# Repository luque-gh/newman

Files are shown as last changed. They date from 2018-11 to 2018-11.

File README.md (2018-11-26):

# Newman alternative - Small scale without mechanical commutator 
## Introduction 
The objective of this project is to **reproduce some claims made by Joseph Newman about his energy machine**.
This will be done in a **smaller scale** compared to the big machine Newman demonstrated.
This machine follows most of Newman's design described in his book.

However, it runs in a much lower voltage **~190VDC** compared to the one demonstrated by Newman (1500+ VDC).
This lower voltage makes possible to use **mosfet transistor and zener diodes** instead of a mechanical commutator.
**Duty cycle and frequency are adjustable** to optimize the performance through a **555 timer**.
Since **Newman's claims timing is very critical** for his invention, this gives much more flexibility to optimize compared to a mechanical commutator.

## Working
**Infrared emitter and sensor are used inhibit or activate the FIRING/BLANK/SHORT OUT cycle** depending on current rotor position.
This machine uses **a solid-state circuit with a 555 timer** to alternate between **FIRING (HIGH)** and **BLANK / SHORT OUT (LOW)**.

### FIRING/BLANK/SHORT OUT Cycle
The first phase is **FIRING** which enable both mosfets to energise the coil through the battery bank.
After that, the **BLANK** phase begins and cut the supply energy from the batteries, collapsing the field from the coil.
The **BLANK** phase only ends when the voltage difference in the coil is above the reverse zener voltage (>400V).
When this voltage is achieved, the **SHORT OUT** begins.
After that, a new **FIRING** phase begins reconnecting the battery bank to the coil again.

The cycle is activated in the range 135° to 225° and determined by the printed part **Commutator-Disc-90Deg**.
Each activation range requires an independent coil and circuit. In the test setup and videos, only one coil is used, but it is possibile to use two coils and activate in the range -45° to 45° as well.

## Schematic

Created using **Fritzing 0.9.3**.

Available in **/schematic**.

## Test Setup
* One coil activated in the range 135° to 225°.
* **~190V VDC** input voltage for the coil (20 x 9V zinc-carbon batteries **OUT OF WARRANTY, BUT NOT DEPLETED**).
* 9V zinc-cabon battery for the circuit controller.
* 555 Duty+ for FIRING is ~82.1%.
* 555 Frequency is ~17.24Khz.
* 2-channels **Rigol DS1052E** Oscilloscope. 
	* Channel A (Yellow) - Batteries voltage
	* Channel B (Blue) - Voltage across 10Ohm resistor before ground (=Amps / 10).

## Preliminary Results

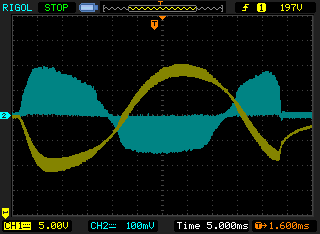
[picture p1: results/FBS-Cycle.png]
Fire/Blank/Short Out cycle


This scope shot show both battery voltage (yellow) and current (blue) in the activation zone.
In the first part, there is energy consumption from the batteries because voltage goes down and current goes up.
However, this trend is averted by **the induced current in the coil from the magnets and from the collapsing magnet field around the coil**.
Current is reversed and voltage recovers and goes even above the batteries charged voltage. So, batteries are being charged in the middle part.
Notice how important is the geometry, because in other machines like the Bedini's SSG, the current induced by the collapsing magnet field goes against the induced current by the magnes, slowing down the machine.
In the last part, the induced current decreases and energy consumption from the batteries is resumed until it leaves the activation zone.

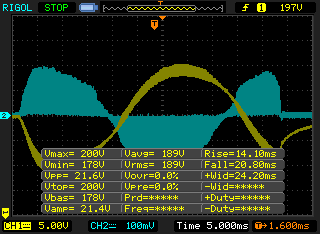
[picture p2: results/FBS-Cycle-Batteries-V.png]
Fire/Blank/Short Out cycle - Voltage


When energy is consumed, batteries voltages goes down to 178V.
When recharge process takes place, batteries voltage goes up to 200V.

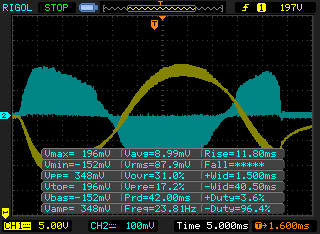
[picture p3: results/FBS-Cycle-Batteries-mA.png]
Fire/Blank/Short Out cycle - Current


Likewise, current goes up to 19.6mA in the consumption and reverse to -15.2mA in the recharge phase
(current must be divided by 10 because we are using 10 Ohm resistor).

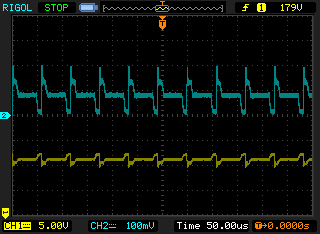
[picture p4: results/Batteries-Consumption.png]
Batteries consumption


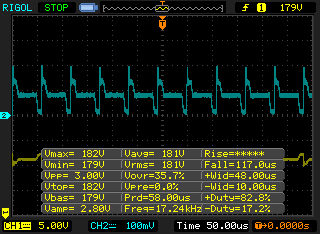
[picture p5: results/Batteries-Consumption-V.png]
Batteries consumption - Voltage


Closeup view to batteries in consumption phase.
Notice the 555 frequency is 17.24Khz which is much higher compared to frequency used by Newman is his experiments.

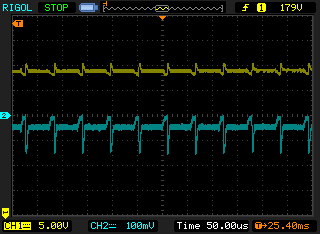
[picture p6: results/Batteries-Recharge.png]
Batteries Recharge


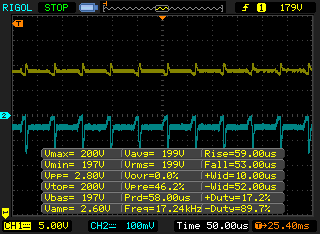
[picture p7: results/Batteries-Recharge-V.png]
Batteries Recharge - Voltage


Closeup view to batteries in recharge phase. Frequency still the same as expected.

Although this is preliminary results, frequency seems to don't matter much except when lower frequencies are used that makes the back emf becames too strong for the rotor to overcome.
On the other hand, duty cycle affects a lot, affecting both the energy consumption, recharge and rpm.
Increasing duty for the FIRING phase increases consumption, recharge and speedup the rotor but not at the same rate. 
So, the exact sweet spot that gives the maximum recharge and rpm and minimum consumption is unknown.

## Conclusions so far...

Although there are too many input variables to deal with:
* Coil's input voltage
* 555's frequency and duty cycle
* Range of the activation zone
* Wire diameter and length
* Magnet size and strength

**It's clear that Newman's invention does recharge the batteries when running**.
Although I am using a solid state circuit instead of a mechanical commutator, it tries to mimic the working of the mechanical commutator described by Newman.
So far, the results that I have achieved are not overunity, but they are at least interesting and they can be improved.

## Things to do in future...

* More tests with different input parameters
* Analyse relation among input and output parameters
* Measure RPM
* Running test with low farad capacitor as input voltage for the coil
* PMBO 2018 using improved geometry

## Building Instructions

### Requirement
* 3D Printer
* Soldering tools
* Hot glue gun

### Assembly itens
* 2 x 6000 Full Ceramic Bearing 10x26x8mm
* 2 x N52 45x45x20mm Block Magnet Strong Rare Earth Neodymium Magnet
* ~5Kg AWG 28 Copper
* ~500g PLA or ABS **(DO NOT USE transparent or white color)**
* 22AWG solid core wire for soldering the IRs

Print all STL files in the directory **/model**.
Put together **Coil.Inner and Coil.Outer** and insert in both holes **Coil.Lock**
Wind all AWG 28 Copper in the coil. There are holes in the coil for up to two coils. It's recommended to fill the whole coil with copper wire. The more, the better.
22AWG must be solderd in IR sensors and emitters (only a par is required for this test). IR sensor and emmiter must be put in **Coil.BL-4xLR** in any spot facing each other.
Glue the IR sensor and emitter with hot glue in the **Coil.BL-4xLR**.

### Circuit items
* 1 x 555 CI
* 1 x 2N2222
* 1 x 2N3906
* 2 x IRF830
* 2 x 1N5388
* 1 x Linear Potentiometer 50K
* 1 x 470k Resistor
* 1 x 47k Resistor
* 1 x 4.7k Resistor
* 1 x 1k Resistor
* 1 x 680 Resistor
* 1 x 4.7 Resistor
* 1 x Breadboard or PCB
* 1 x 1nF Capacitor
* 1 x 10nF Capacitor
* 1 x 10uF Electrolytic Capacitor
* 1+ x IR TIL32
* 1+ x IR TIL78
* 21+ x 9V Zinc-Carbon Battery

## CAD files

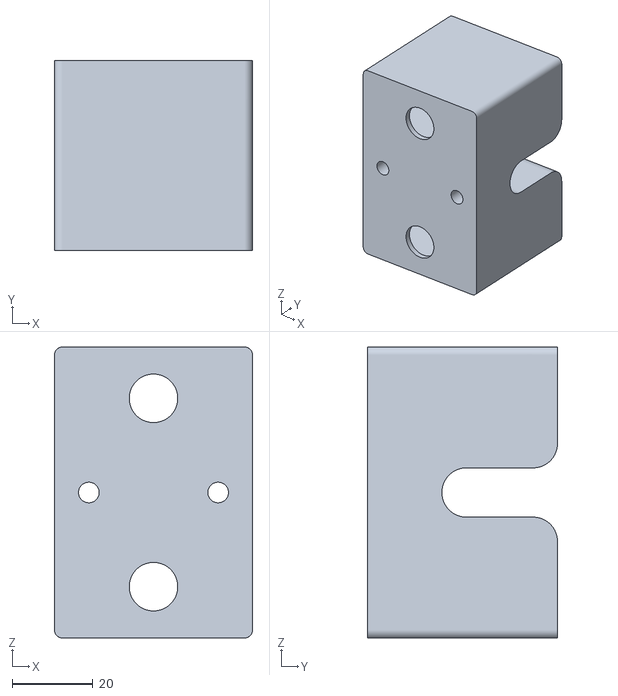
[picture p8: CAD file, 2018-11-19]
model/Magnet.Base.45x45x20.stl
49.0 x 47.0 x 72.0

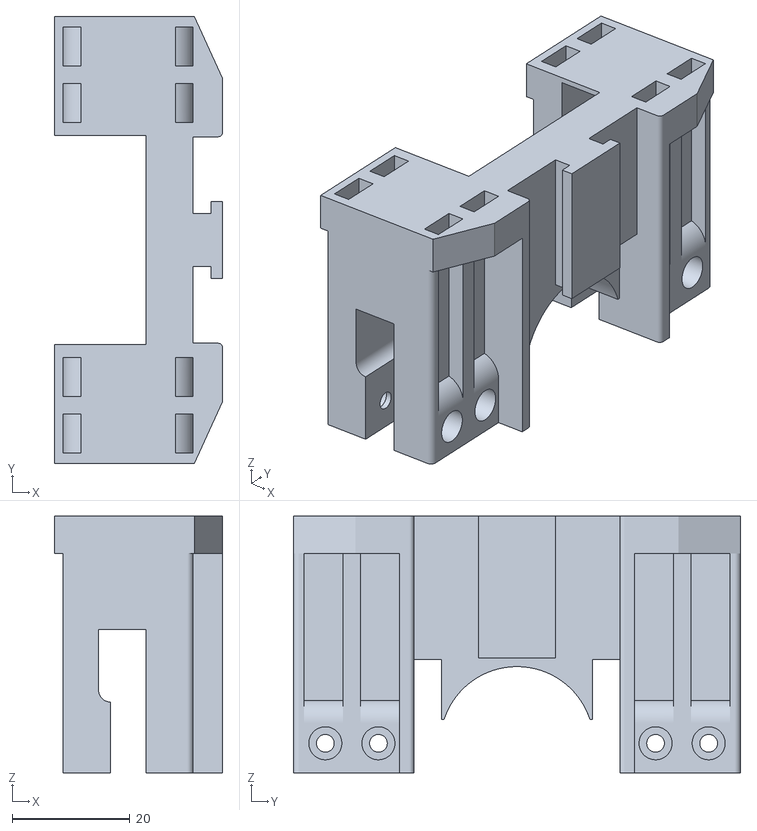
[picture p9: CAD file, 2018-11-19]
model/Coil.BL-4xLR.stl
28.5 x 75.8 x 43.5

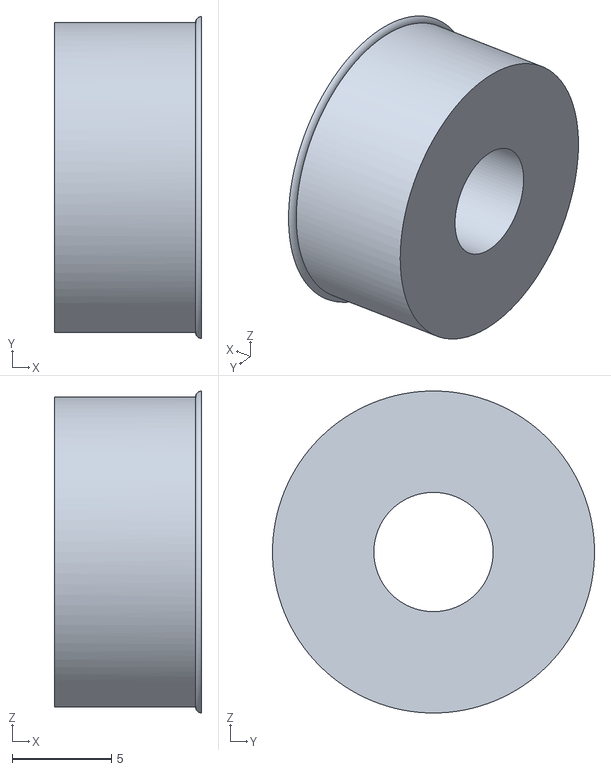
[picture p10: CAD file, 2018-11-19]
model/Coil.Lock.stl
7.40 x 16.2 x 16.2

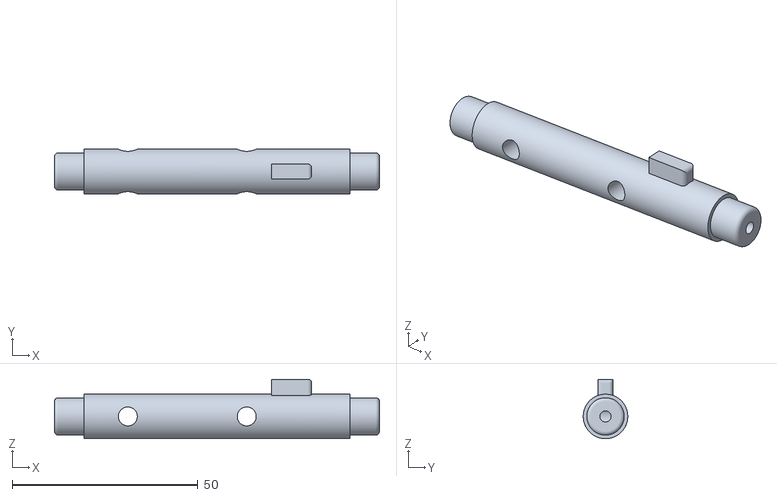
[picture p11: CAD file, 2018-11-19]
model/Rotor.Axis.stl
87.5 x 12.0 x 16.0

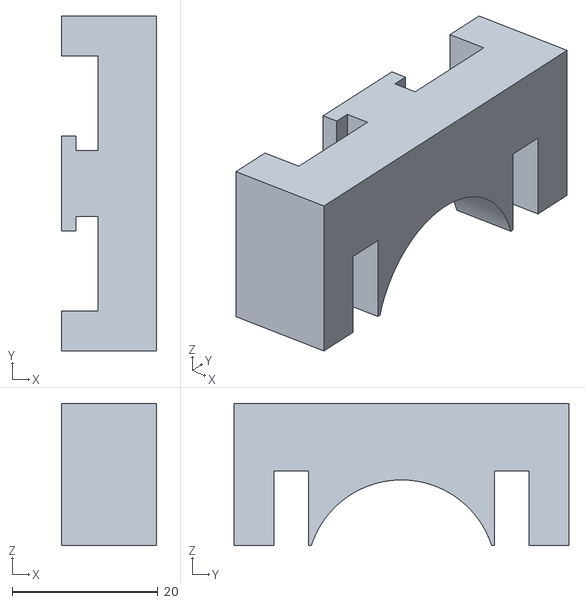
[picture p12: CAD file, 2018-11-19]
model/Coil.BL.stl
13.0 x 46.0 x 19.5

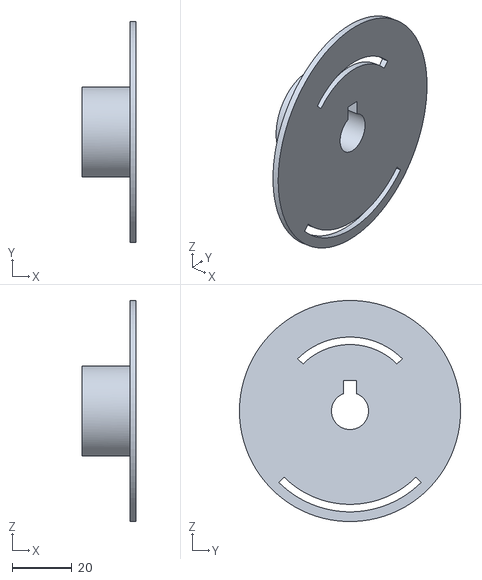
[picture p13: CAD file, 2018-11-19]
model/Commutator-Disc-90Deg.stl
18.0 x 74.0 x 74.0

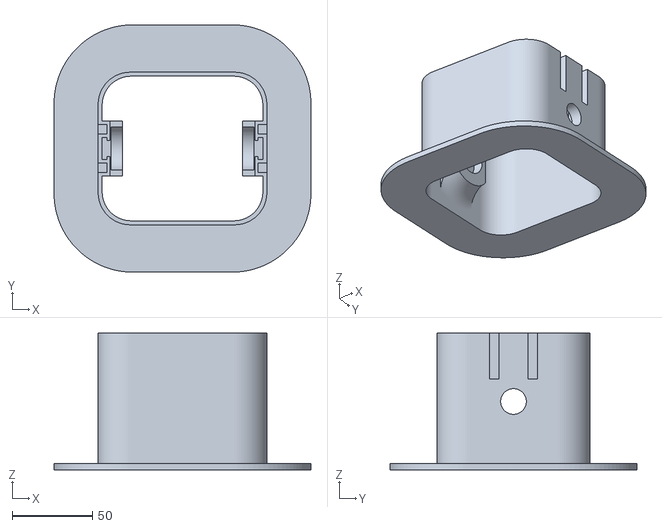
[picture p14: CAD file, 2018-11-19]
model/Coil.Inner.stl
160.0 x 154.0 x 85.0

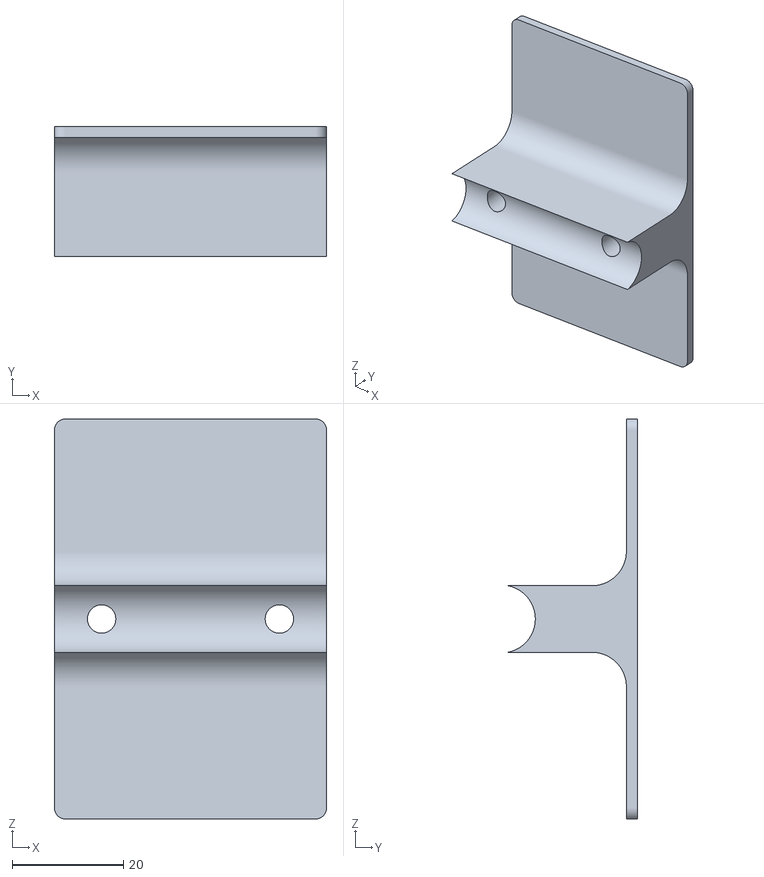
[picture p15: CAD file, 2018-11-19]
model/Magnet.Cap.45x45x20.stl
49.0 x 23.4 x 72.0

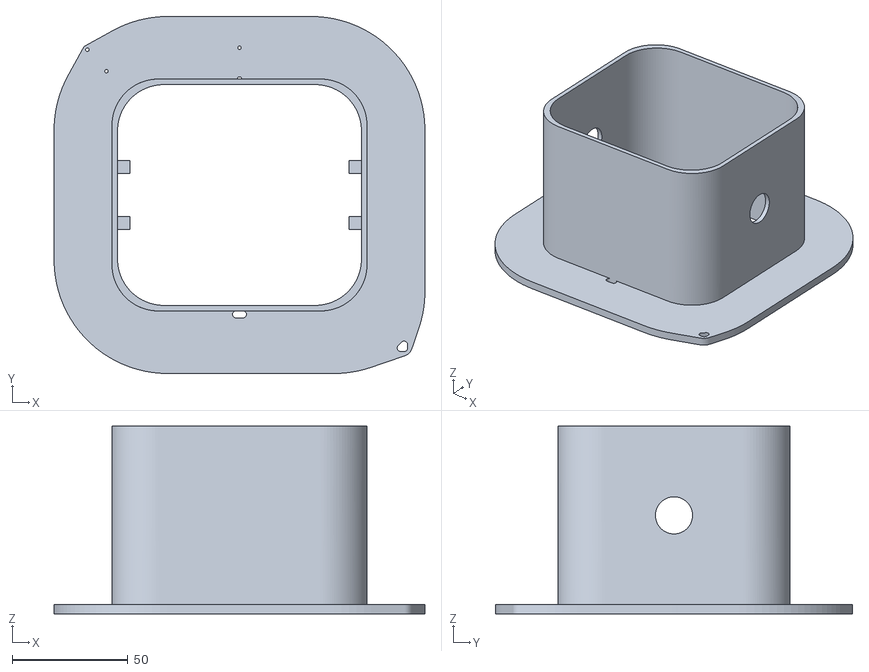
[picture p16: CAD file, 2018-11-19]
model/Coil.Outer.stl
160.0 x 154.0 x 81.0
